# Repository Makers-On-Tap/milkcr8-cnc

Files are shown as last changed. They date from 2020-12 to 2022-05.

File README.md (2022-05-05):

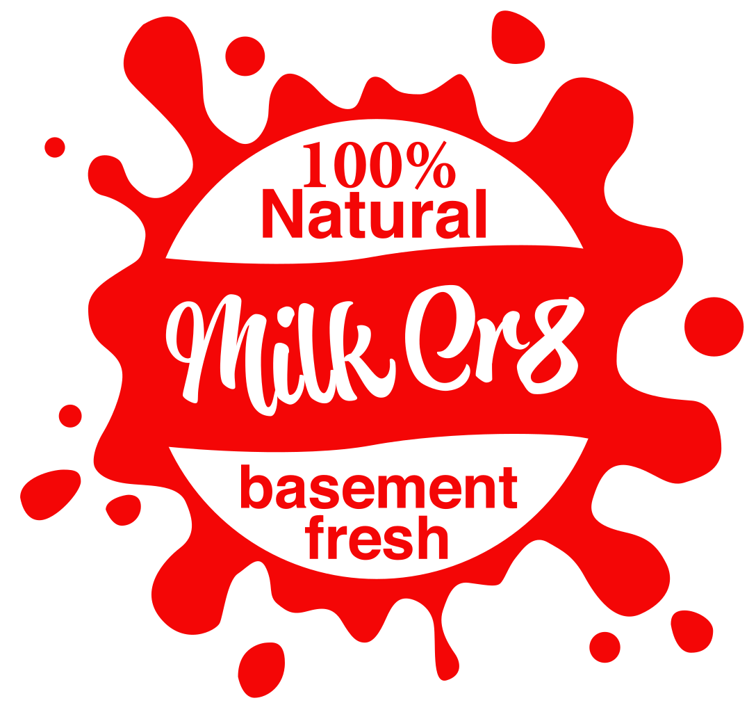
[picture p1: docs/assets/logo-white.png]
milkcr8_logo


# Welcome to the Milk Cr8 CNC Project
Home of the Milkcr8 Desktop CNC Machine!

Check out the [documentation site](https://www.milkcr8cnc.com)

This project uses mkdocs-material for the theme, the [reference guide for supported markdown features is available here](https://squidfunk.github.io/mkdocs-material/reference/#configuration)

Documentation files are located under the `docs` folder

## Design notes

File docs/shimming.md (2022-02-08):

# Shimming and Flattening the X Tube

The hot rolled mild steel tubing used for the X axis (and the Y axis) isn't always flat enough on the wide face for perfect mounting of the rails without some extra work. 

In one trial, there was variance of 0.01 inches across the wide face of the tube, with about 0.007" of variance over the width of the rail. 

First, we recommend checking each side to see if one is flatter than the other. Check it with a straight edge, and look for light coming through under the blade of the straight edge.

What looks like a small bump on the edges will still add up to too much difference in rail flatness to mount the Z axis without binding the rails.

## Ways to Mount the Rails Flat

Luckily, there are a few options if your X tube isn't flat.

1. Get someone to mill the face of your tube flat. 
2. Use epoxy to level the face of your tube.
3. Shimming the rails. (this is what we're talking about here)

## Shimming the Rails

Luckily, shimming the rails isn't hard, and can be done stably with commonly available materials.

Most grocery stores will sell [heavy duty aluminum foil](https://www.reynoldsbrands.com/products/aluminum-foil/heavy-duty-foil). 

This is inexpensive (though more expensive than regular aluminum foil) and is consistently 0.001" in thickness.

Aluminum soda cans have a thickness of 0.004". Soda can walls will be very sharp when cut, so proceed with caution.

The rails are 12mm wide, with a clearance of 3.5mm in the center for the M3 screws. So the width of the shim needn't be much wider than 4.25mm (12mm / 2 - 3.5mm / 2)

### Shimming With Foil

Fold a length of foil in half, and insert the folded seam under the low side of the rail. 

If you have a dial indicator, tighten a section of the rail and check the flatness over the short dimension of the top face. Loosen and add more shims as needed. Tightening screws before each measurement, and loosening to add more shim material.

### Shimming With Soda Cans

Cut the top and bottom off the can, and make one straight cut up the side so you can unroll the can flat. Use acetone to clean off the food-safe lining from the inside, and remove any ink that will come off the outside. 

Cut the can into 4-5mm wide strips, so the long edge is the circumference of the can. You should be easily be able to get eight strips from a standard can, which is enough for two strips under the entire length of each 300 mm rail. 

Insert one shim under the low side of the rail. Tighten, and measure. Add additional stock if needed, and repeat measurements until the rail is mostly flat along it's short dimension of the top face.

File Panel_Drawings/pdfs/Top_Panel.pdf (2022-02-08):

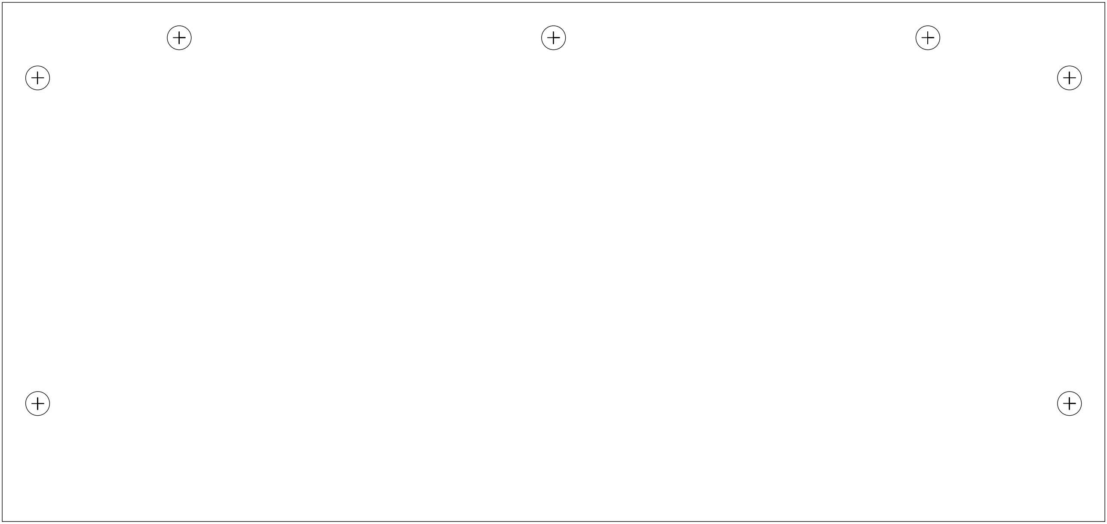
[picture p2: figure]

138mm

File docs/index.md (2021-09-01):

# Welcome to the MilkCrate CNC Project!

This site contains all the info and instructions you'll need to build your own desktop CNC mill!

If you're new to the project, check out the [About](about.md) page to learn the backstory of the MilkCrate CNC.

If you have some questions about it, check out our [FAQ](faq.md) page! Your question is most likely answered there.

Development and discussion of the project is done in the MilkCr8 CNC Discord server. https://discord.gg/qguQRYZAea

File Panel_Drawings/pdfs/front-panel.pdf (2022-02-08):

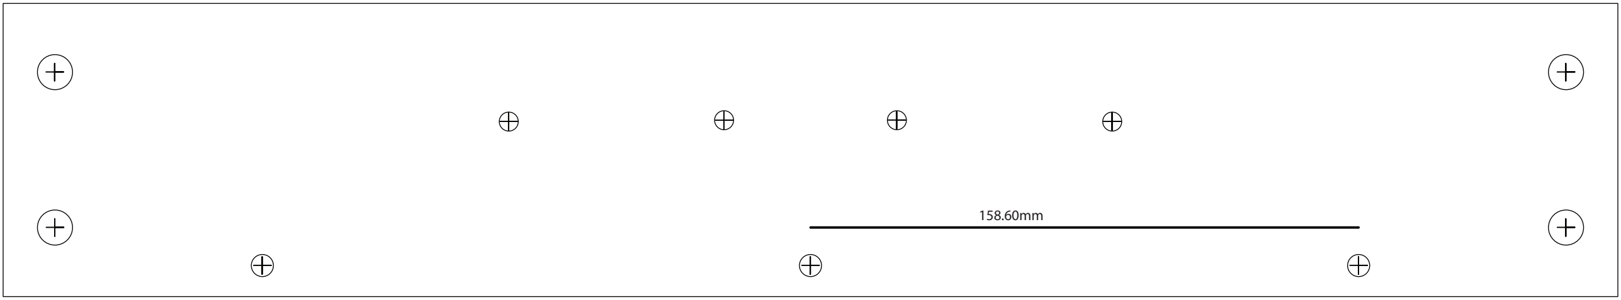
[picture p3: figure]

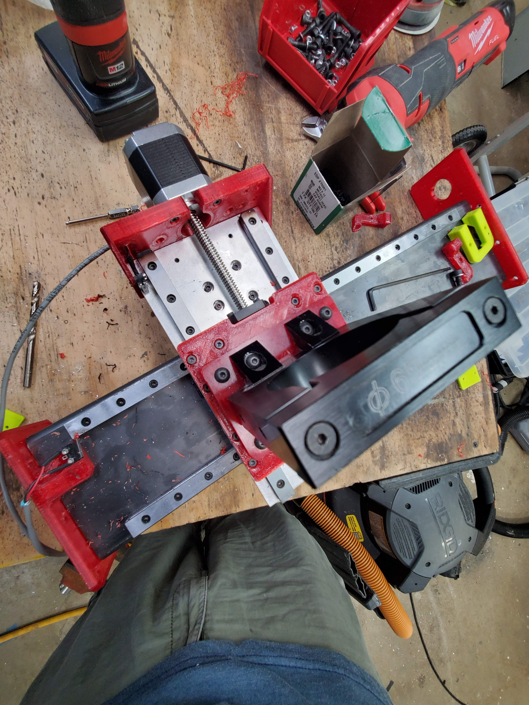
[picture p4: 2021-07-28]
docs/assets/images/img/xz_sub6.jpg

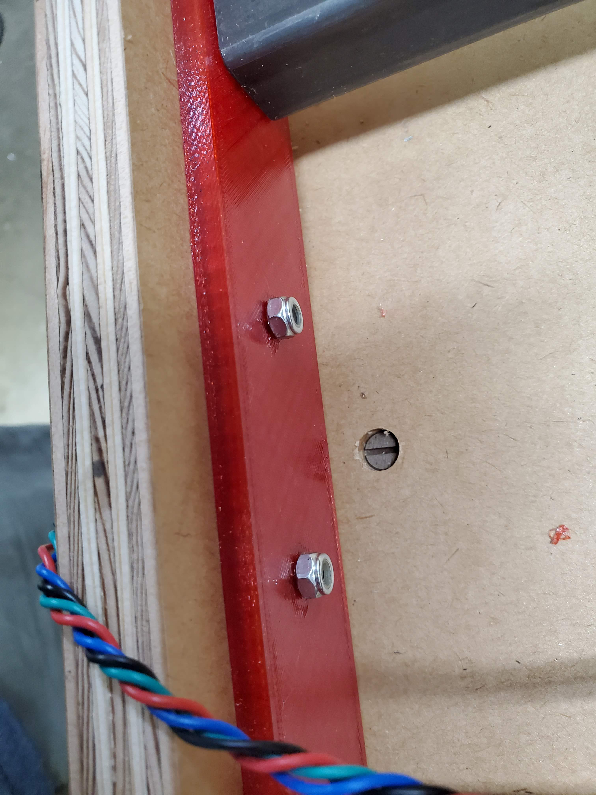
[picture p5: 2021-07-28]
docs/assets/images/img/y_box2.jpg

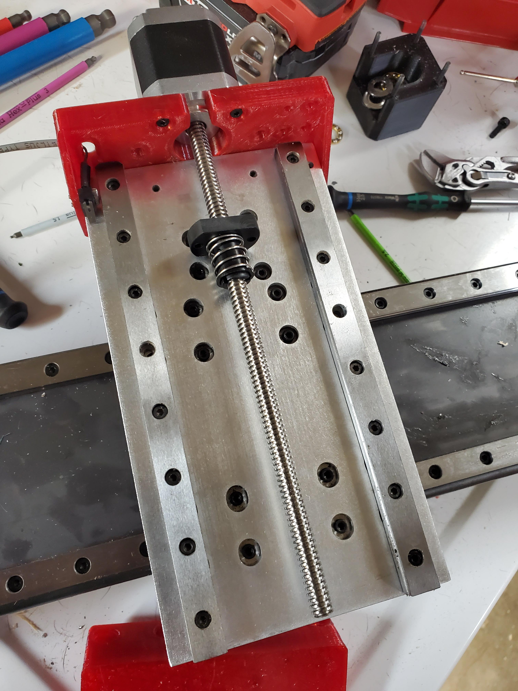
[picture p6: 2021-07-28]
docs/assets/images/img/xz_sub1.jpg

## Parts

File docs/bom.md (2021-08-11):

# Bill of Materials
Current BOM can be found in this [read only Google Sheet](https://docs.google.com/spreadsheets/d/1ViruGe-mIjATBrFZ_2N3Xh3YK8Kv0xZOzpvj6fFhka0/edit?usp=sharing). The BOM is considered semi-stable and but safe to order from.

# Source files and STL's
All parts to be made can be found here https://github.com/Makers-On-Tap/milkcr8-cnc

# Printed Parts List
All the non-jig [printed parts](https://github.com/Makers-On-Tap/milkcr8-cnc/tree/main/printed%20parts) are print 1 of each, unless otherwise noted in the filename (i.e. Hinge_6x.stl is 6 units)

You'll need two of each [jig](https://github.com/Makers-On-Tap/milkcr8-cnc/tree/main/printed%20parts/JIGS)

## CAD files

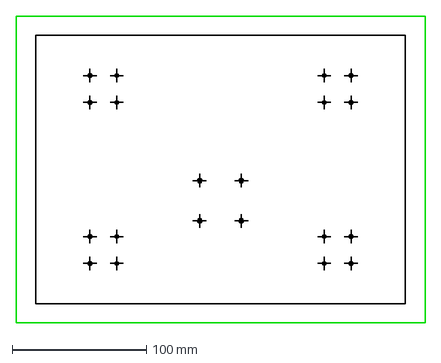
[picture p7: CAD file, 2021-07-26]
Panel_Drawings/dxf/bed_punch_template.dxf
304.8 x 228.6 mm

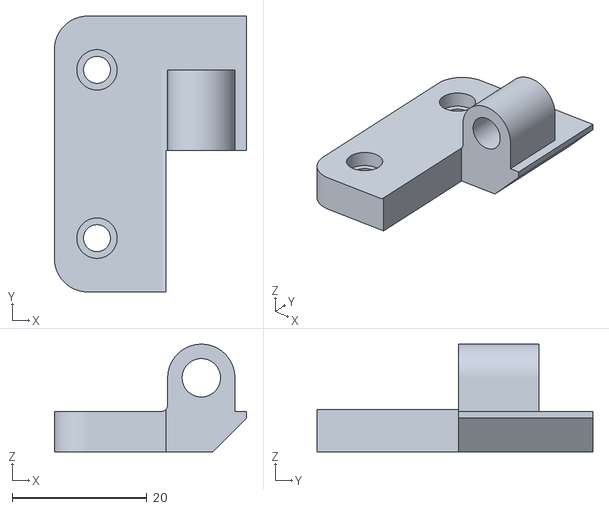
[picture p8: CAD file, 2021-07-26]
printed parts/Hinge_6x.stl
28.6 x 41.0 x 16.0

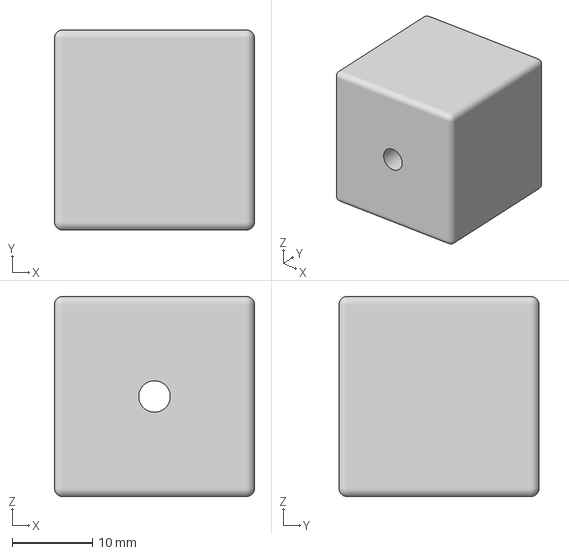
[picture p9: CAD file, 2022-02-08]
printed parts/JIGS/M3TapGuide0.4mm.3mf
25.0 x 25.0 x 25.0 mm

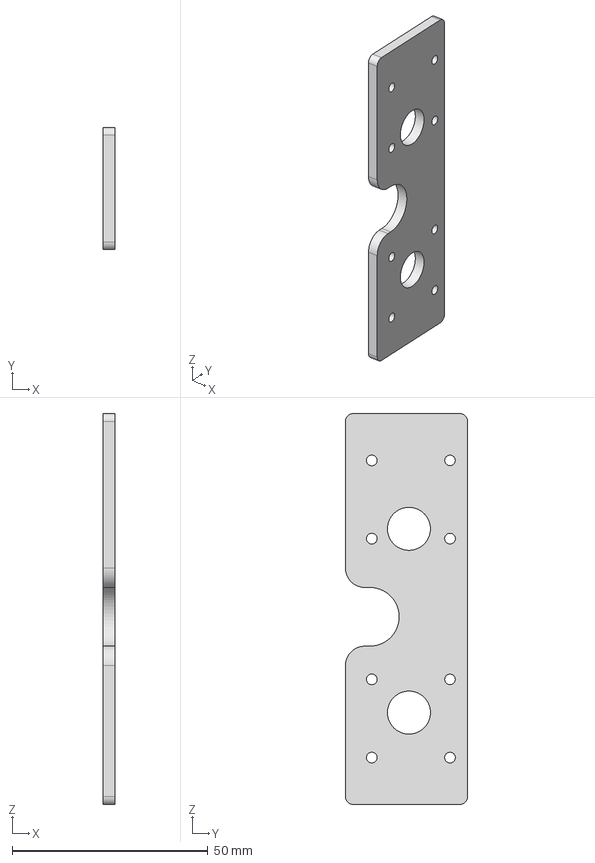
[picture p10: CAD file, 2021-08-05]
printed parts/STEP/Z_Spacers_x2.step
3.18 x 31.3 x 100.0 mm

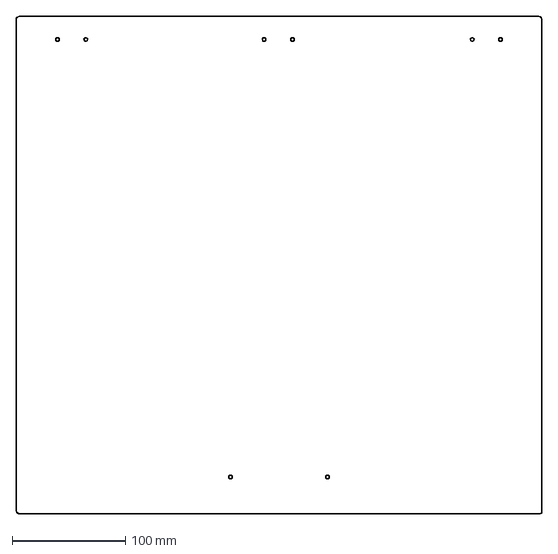
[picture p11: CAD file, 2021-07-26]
Panel_Drawings/dxf/Window_qtr_in_acrylic.dxf
464.0 x 439.0 mm

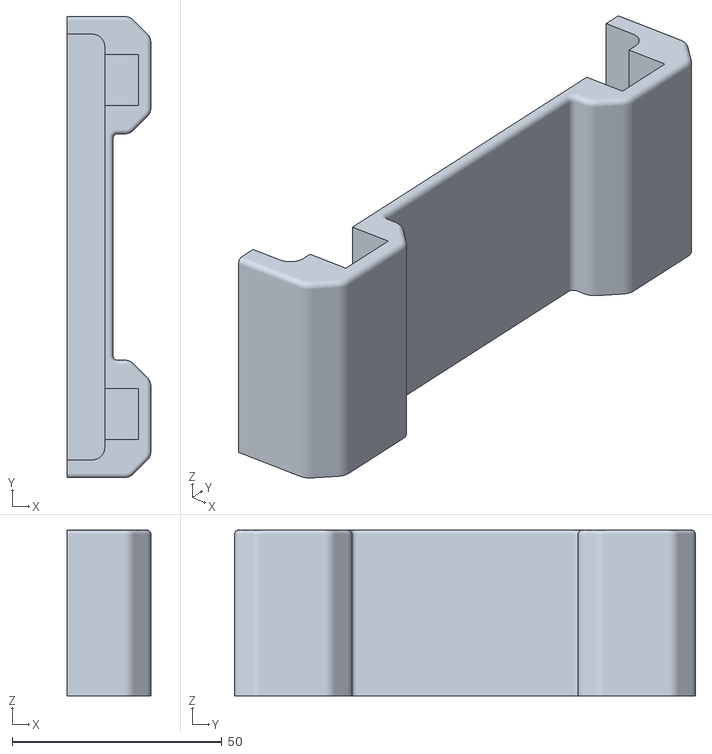
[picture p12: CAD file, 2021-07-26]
printed parts/JIGS/Jig_X_Rail_x2.stl
20.0 x 110.0 x 39.6

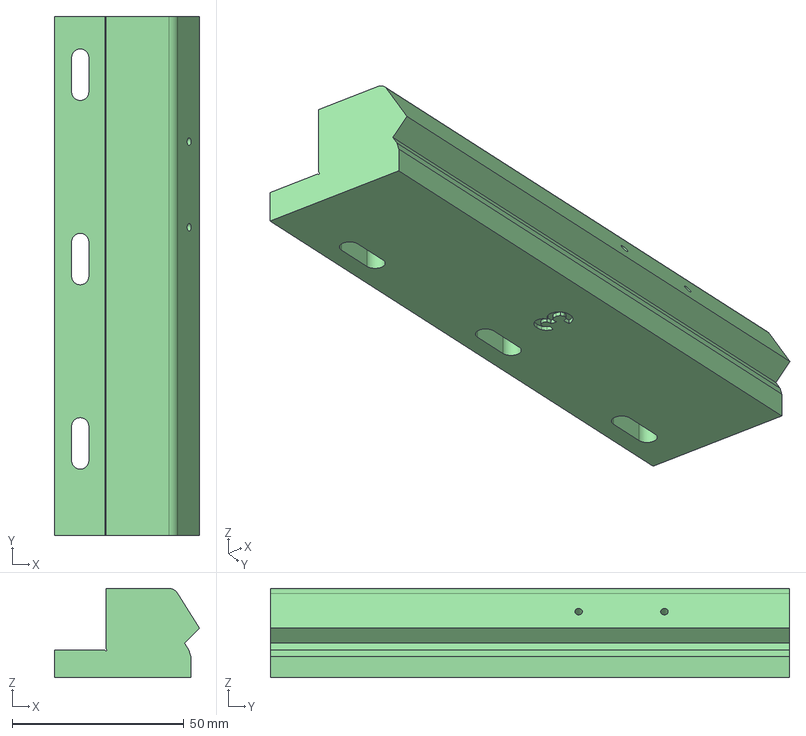
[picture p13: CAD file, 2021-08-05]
printed parts/STEP/WinMountTop_Right3.step
42.3 x 151.4 x 26.0 mm

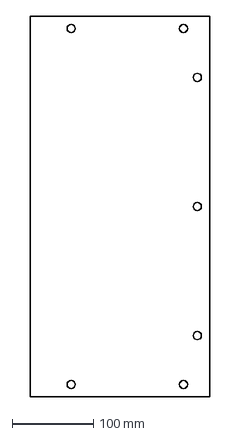
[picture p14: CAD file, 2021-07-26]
Panel_Drawings/dxf/Top_Panel.dxf
220.0 x 467.2 mm

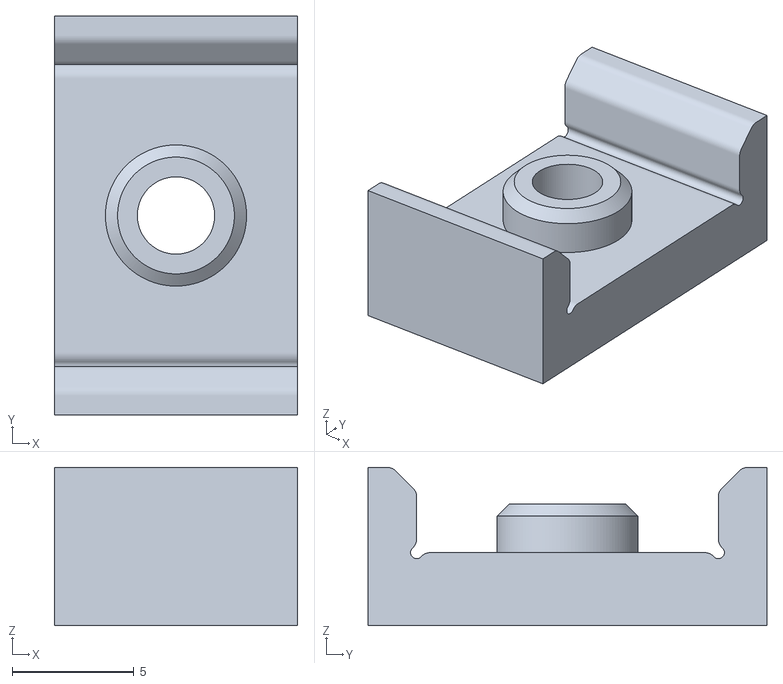
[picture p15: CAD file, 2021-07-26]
printed parts/JIGS/Jig_RailPunch.stl
10.0 x 16.4 x 6.50

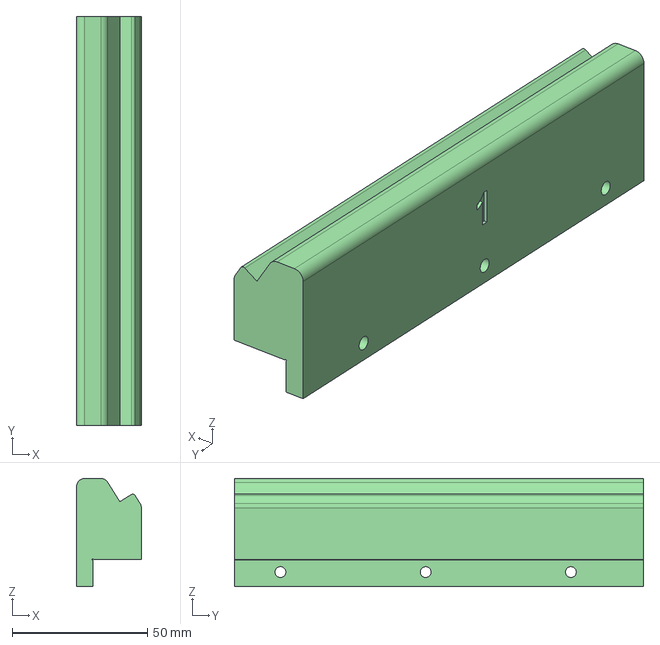
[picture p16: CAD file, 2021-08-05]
printed parts/STEP/WinMountBot_Left1.step
24.0 x 151.4 x 40.0 mm

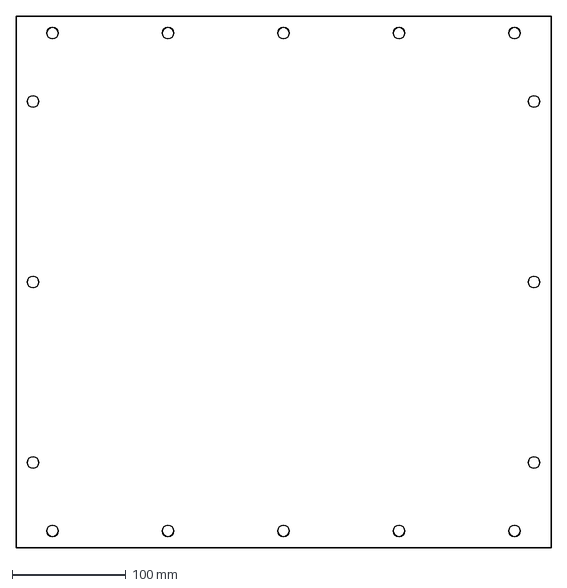
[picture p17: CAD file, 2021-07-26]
Panel_Drawings/dxf/Bottom_panel.dxf
469.9 x 467.2 mm

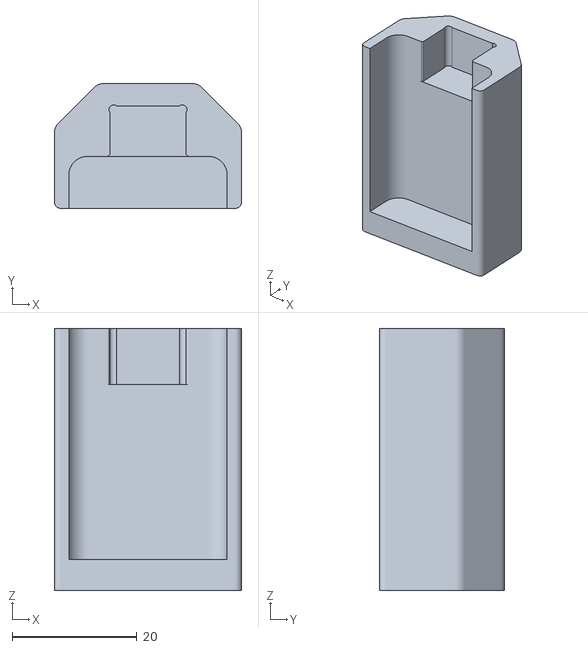
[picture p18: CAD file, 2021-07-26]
printed parts/JIGS/Jig_Y_Rail_x2.stl
30.0 x 20.0 x 42.0

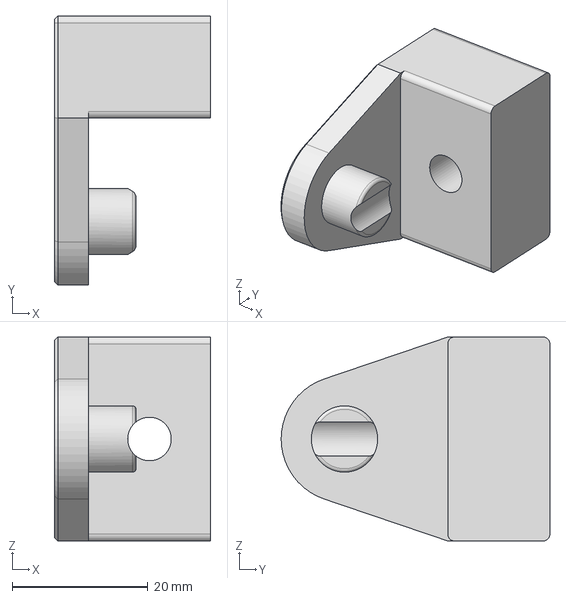
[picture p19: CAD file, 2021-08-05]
printed parts/STEP/Jig_Dowel_Pins.step
23.0 x 39.5 x 30.0 mm

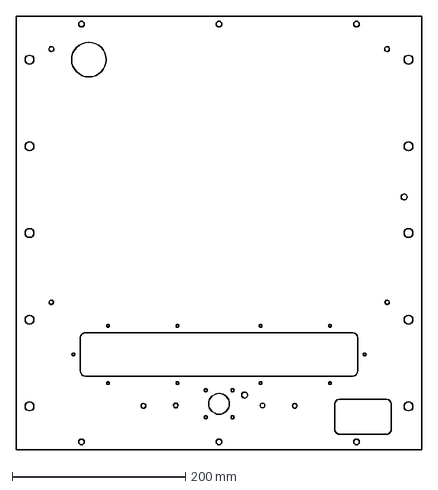
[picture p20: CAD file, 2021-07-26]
Panel_Drawings/dxf/Back_panel.dxf
467.2 x 500.0 mm

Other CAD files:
printed parts/JIGS/Jig_Dowel_Pins_18MM_ply.stl
Panel_Drawings/dxf/Front_panel.dxf
printed parts/STEP/Jig_RailPunch.step
Panel_Drawings/dxf/side_panel.dxf
Panel_Drawings/dxf/Motor_side_panel.dxf
printed parts/DustCover_Left.stl
printed parts/DustCover_Right.stl
printed parts/STEP/DustCover_Left.step
printed parts/STEP/DustCover_Right.step
printed parts/STEP/Hinge_x3.step
printed parts/STEP/Jig_X_Rail_x2.step
printed parts/STEP/Jig_Y_Rail_x2.step
printed parts/STEP/Vac_Port.step
printed parts/STEP/WinMountBot_Mid2.step
printed parts/STEP/WinMountBot_Right3.step
printed parts/STEP/WinMountTop_Left1.step
printed parts/STEP/WinMountTop_Mid2.step
printed parts/STEP/Window_Handle.step
printed parts/STEP/X_Lead_Nut_Mount.step
printed parts/STEP/X_Thrust_Block.step
printed parts/STEP/X_Tubes_LeftIdler.step
printed parts/STEP/X_Tubes_RightMotor.step
printed parts/STEP/Y_Lead_Nut_Mount.step
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

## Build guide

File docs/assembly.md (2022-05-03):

# Assembly

## Table of Contents

* [Prep Work](#Prep-Work)
	* [Tapping and Assembling the X and Z Axis Assembly](#x-and-z-axis-sub)
	* [Assembling the X and Z Axes](#assembling-the-z-and-z-Axes)
* [Making the Cr8](#cr8-atart)
	* [Cr8 Assembly](#cr8-assembly)
* [Y Axis Start](#y-axis-Start)
* [Window](#window)
* [Spindle Mount](#spindle-mount)

## Prep Work

Read through all the directions before you start. You can batch out a few things, like drilling and tapping before you do assembly. Other items are more sensitive to order. We've tried to point that out when it may not be obvious. 

3d-print all your 3D printed parts per the [instructions](printing.md).

Make sure you have two of all the jigs marked 2x in the Fusion360 Project. Pre-drill all the holes. Most can be predrilled with a 1/4" bit. Use an 1/8" bit for smaller holes. The only holes that should be pre-drilled smaller than 1/8" are for the M2 screws that hold in the limit switches.

## X and Z axis Sub

### Punch, Drill and Tap the X-Axis 

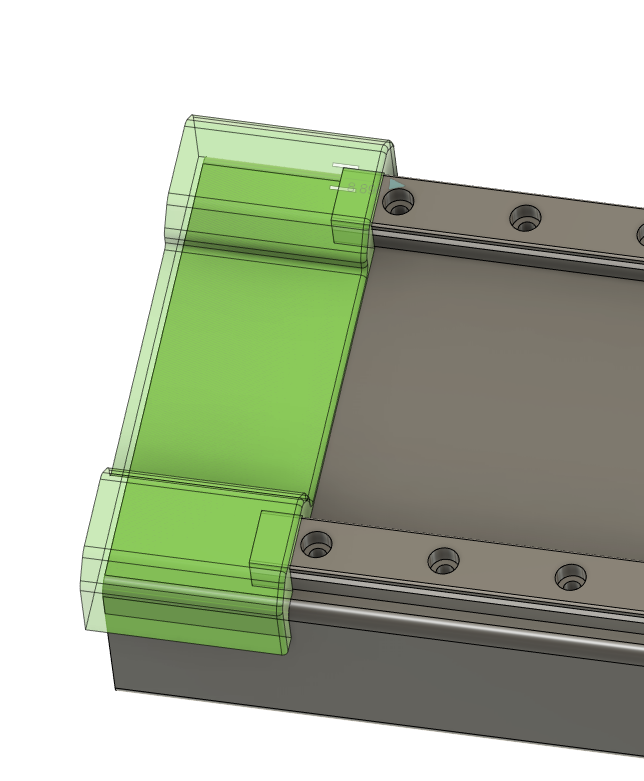
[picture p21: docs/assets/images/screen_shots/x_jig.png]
x_jig


Take a look at your 4x1.5x18" steel tube and see if one side is flatter along the 4" length than the other.

If one side is noticeably flatter, set up your printed X-Axis jigs and linear rails on that side. 

We recommend using a 3.5 mm transfer punch to make a light mark for each of the holes, and then enlarging those holes slightly with a center punch. 

Drill all 16 holes for each rail, and tap with an M3 0.5 tap and plenty of tapping fluid. There is an M3 tap guide in the jigs folder on the github to help keep the tap straight. You may have to adjust the scale slightly depending on the settings and nozzle size on your 3D printer.

At this point, you can start screwing down your rails to the tube with M3x10 SHCS and check if the rails are flat. It's not uncommon for the rails to both be tilted in toward the center of the axis. If this is the case (or if they are otherwise out of parallel with each other) check out the [shimming](shimming.md) guide.

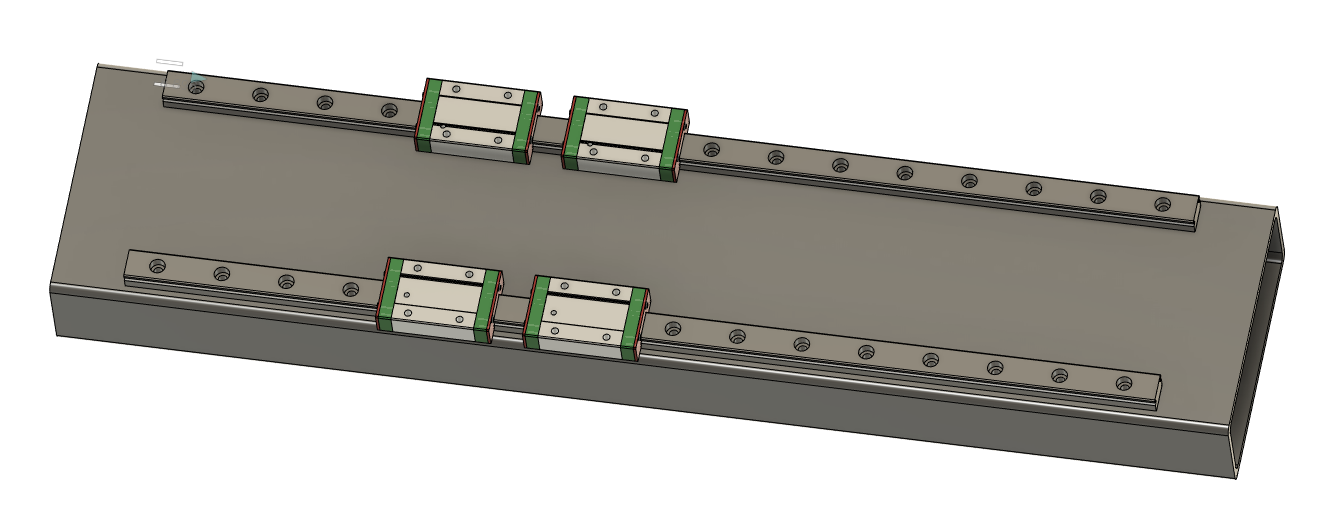
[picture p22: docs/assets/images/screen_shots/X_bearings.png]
x_bearings


### Assembling the X and Z Axes

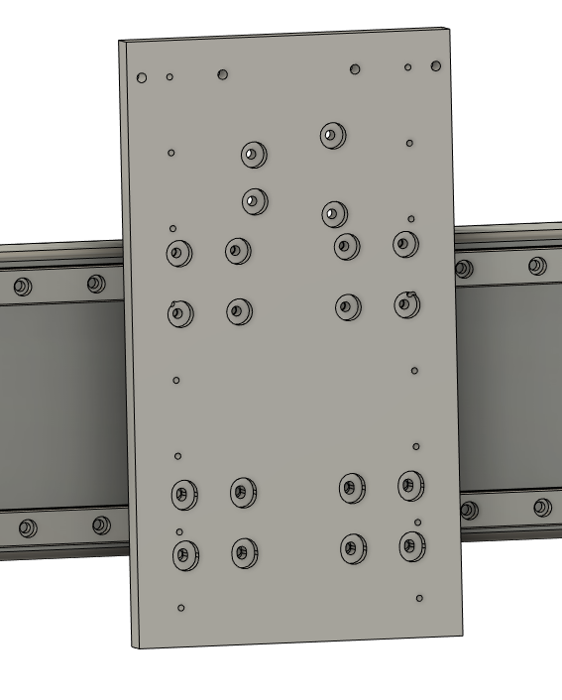
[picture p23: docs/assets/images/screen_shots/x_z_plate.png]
x_z_plate


Use 16 M3x10 SHCS to bolt the Z to X Plate to the carriages.  

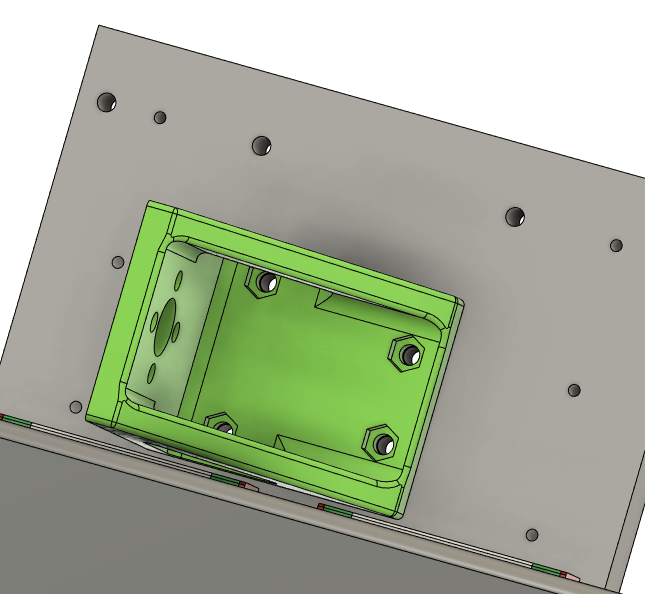
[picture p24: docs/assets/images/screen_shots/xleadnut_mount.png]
x_leadnut


M3 nuts pressed into X Lead Nut Mount.
M3x12 SHCS to bolt the X Lead Nut Mount to Z to X plate.

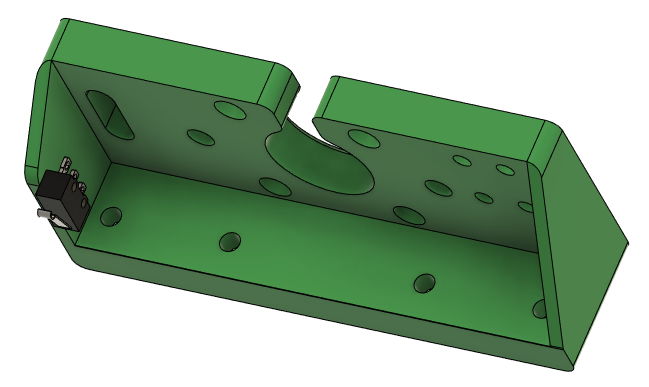
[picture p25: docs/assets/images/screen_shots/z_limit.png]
Z_limit


M2x12mm bolts to attach the limit switch to the Z Linear Motor Mount. You cannot attach the limit switch once the Z Motor Mount is attached to the Z to X Plate.
Solder wires before bolting. The "Normally Closed" (NC) configuration is recommended for best safety practices.
Run wire for the Z limit switch through slot in the Z Linear Motor Mount. 

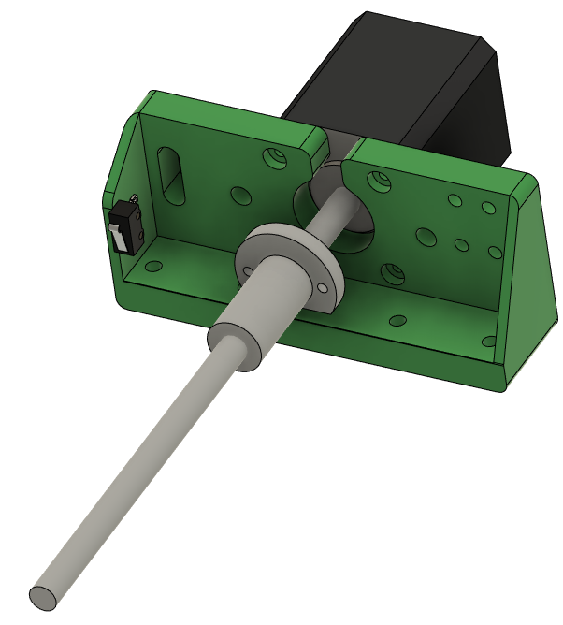
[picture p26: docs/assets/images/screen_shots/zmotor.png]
Z_motor


M3x10 screws into motor, through the Z Linear Motor Mount. You cannot attach the Z Motor after the Linear Motor Mount is attached to the Z to X Plate.  
Make sure lead nut is mounted now, it's a real pain to mount it later. 

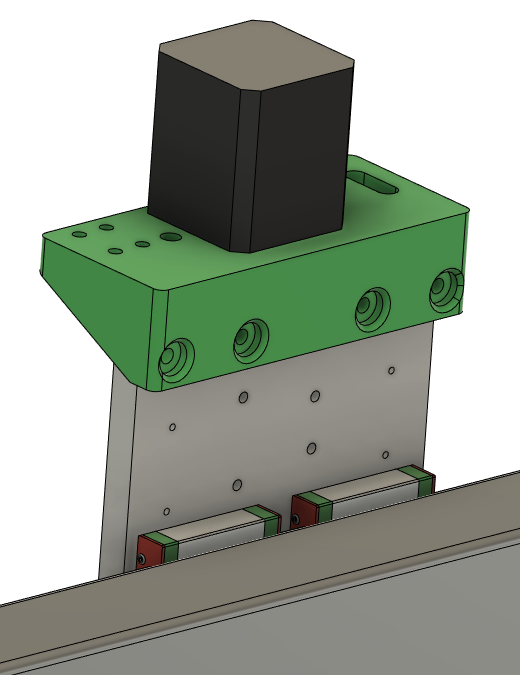
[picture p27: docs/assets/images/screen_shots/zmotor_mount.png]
Z_motor_mount


M4x12 SHCS to through the Z Linear Motor Mount to the Z to X Plate  
Use M4 self tapping screws if using plastic plates

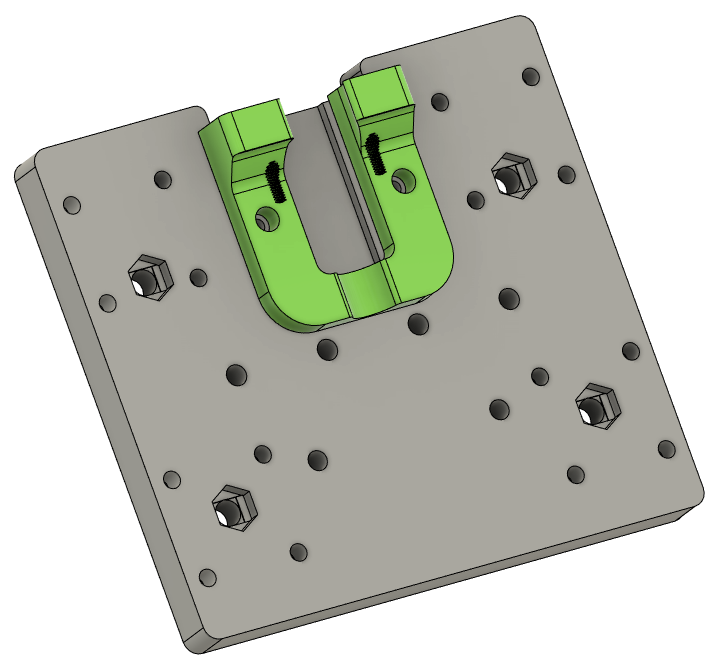
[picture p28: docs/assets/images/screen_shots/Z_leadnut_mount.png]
Z_leadnut


Use M4x12 SHCS to attach the Z Lead Nut Mount to the Z Plate.
Insert M5 nylock nuts into the Z Plate now. It is impossible to insert these once the Z Plate is mounted on the carriage. If they are loose, you can hold them in place with M5 screws until you attach the tram plate and router mount.

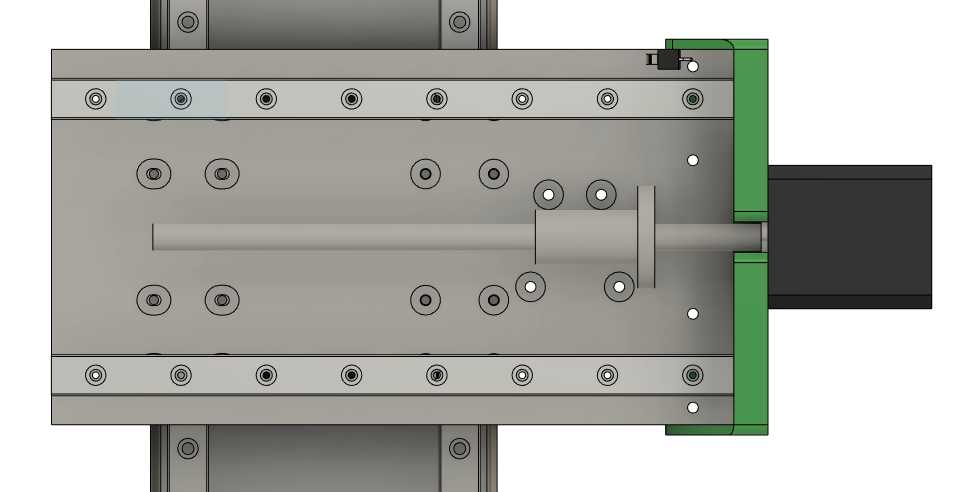
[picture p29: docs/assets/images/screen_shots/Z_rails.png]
Z_rails


Use M3x10 SHCS, or M3 self-tapping screws to attach the Z Linear Rails to the Z Plate.

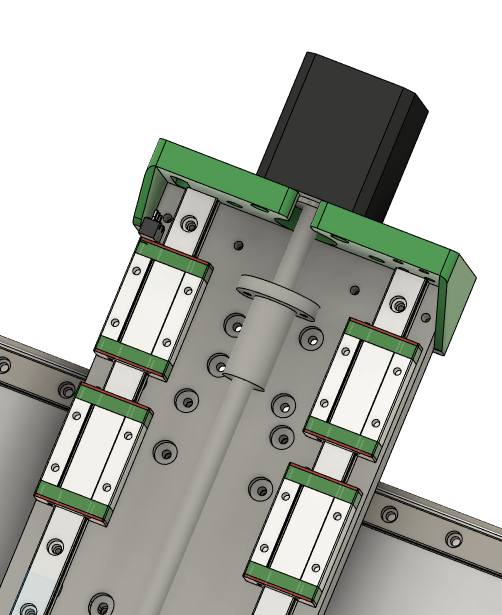
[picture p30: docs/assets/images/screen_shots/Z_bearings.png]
Z_bearings


Put two Z bearings on each Z rail.

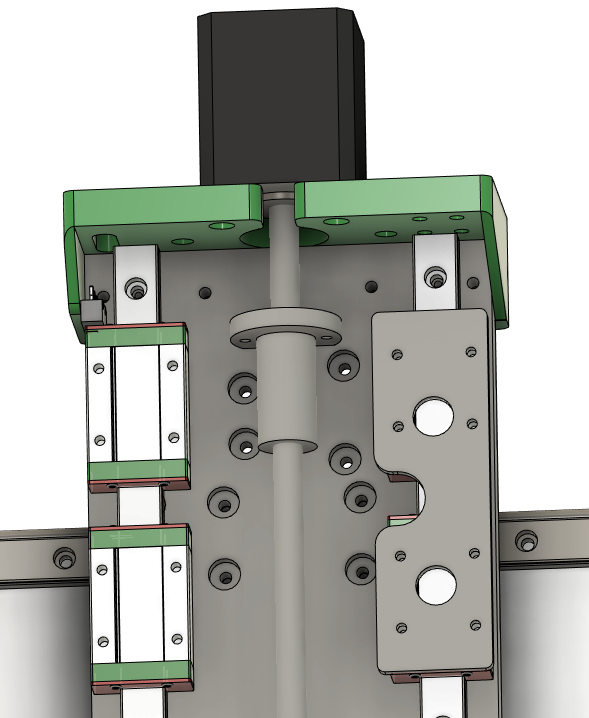
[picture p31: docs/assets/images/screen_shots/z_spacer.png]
Z_spacer


Put 1 Z Spacer over each set of bearings.
Drill out the bolt holes if needed to make sure the M3 bolts slip through cleanly  

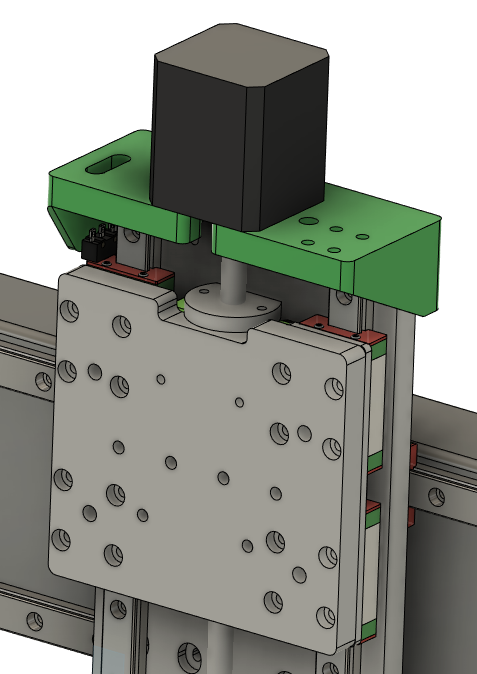
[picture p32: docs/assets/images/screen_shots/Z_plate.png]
Z_plate


Use M3x10 SHCS attach the Z Plate to the bearing blocks through the spacers.

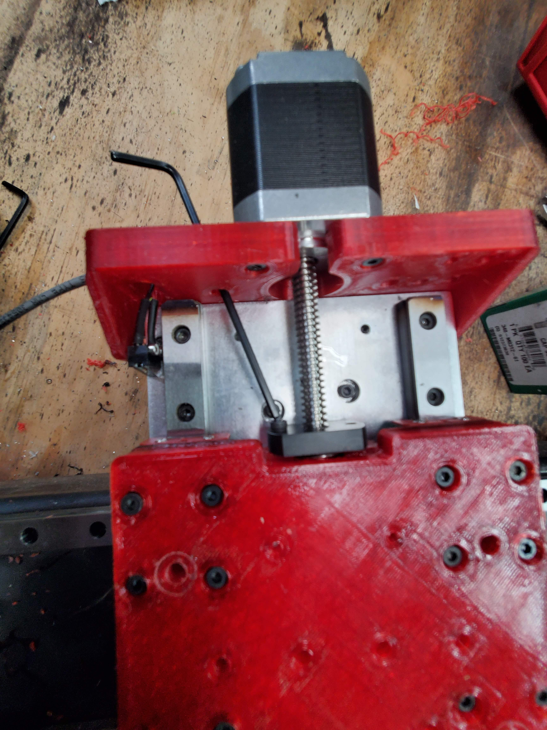
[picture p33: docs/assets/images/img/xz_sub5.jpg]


Use M3x10 SHCS tp attach the Z Lead Nut Mount to the Z Plate. Use the holes in Z Linear Motor Mount to slip allen key through and access bolts. You may have to rotate the lead screw to properly align the Z Lead Nut Mount in order to screw in the bolts.

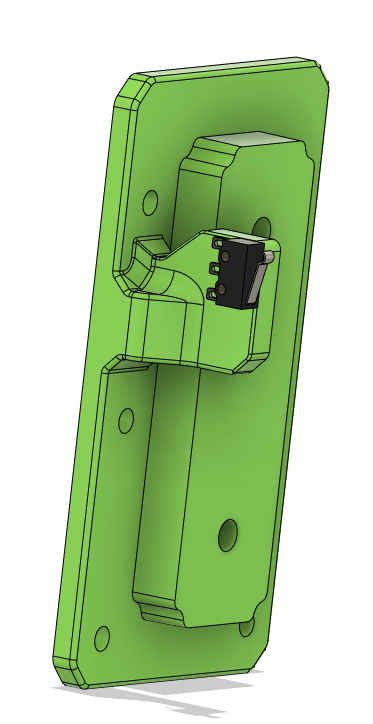
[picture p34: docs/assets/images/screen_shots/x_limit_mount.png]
X_limit


Solder the wires to the X limit switch and attach the X limit switch to the X Tube Left Idler with M2 screws. Do not attach the left X Tube Left Idlder to the X Tube at this time.

## Cr8 Start

Check the length of your X-tube. Midwest Steel has a tendency to cut the tubes 1/8" long. So you'll either need to file that down, or increase the width of the front, back, top, and bottom by 1/8" to compensate. 

A soft recommendation is to get the crate parts cut on a CNC. There are a lot of holes to drill and it's easier to get them all aligned if it's done by a computer. That said, there are also large format [PDFs](../Panel_Drawings/pdfs) to print and attach to the panels with spray adhesive that work as good guides. It's very possible to make it with hand-drilled holes in the crate, it's just harder.  

### Cr8 Assembly

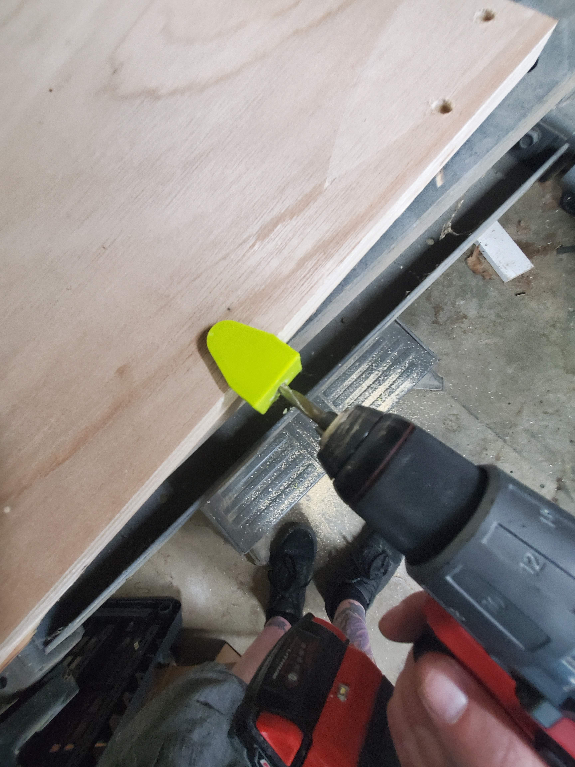
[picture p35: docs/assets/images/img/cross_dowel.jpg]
Cross Dowel


Use the dowel jig in the large holes on the frame drill the holes on the edge that the 1/4" bolts will go through and thread into the dowel nuts.

Drill the holes about 10mm past the dowel nut hole to allow for bolt clearance

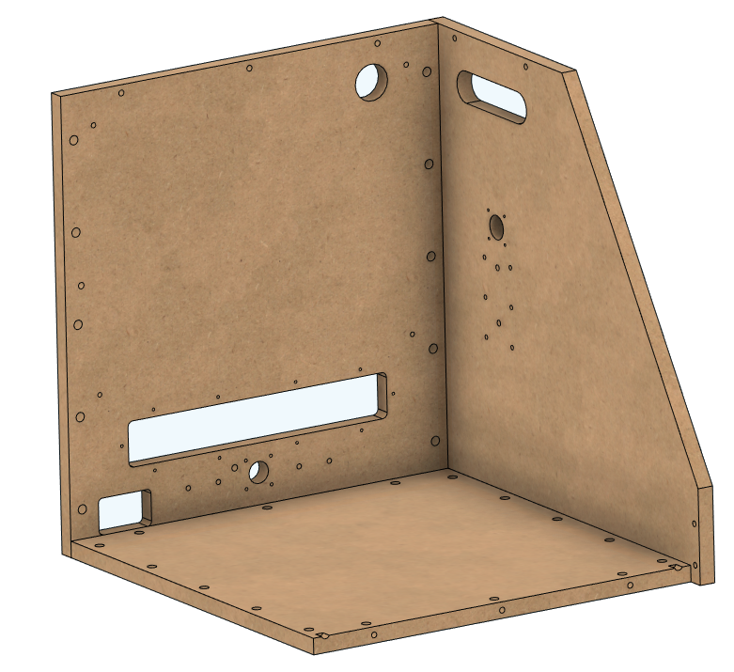
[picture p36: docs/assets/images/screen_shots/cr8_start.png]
Cr8


Build up Cr8 with 3 sides like this, the right side (from the front), the bottom, and back.

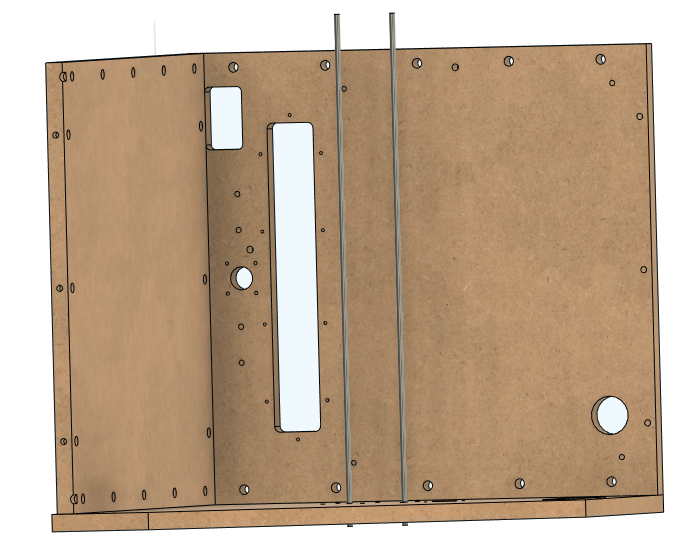
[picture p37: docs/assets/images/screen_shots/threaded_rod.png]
X-tension


Put lock washer, and nuts on one end of each of 2 threaded rods  

Put the two threaded rods through the X holes on the right side of the crate.

Lie the crate on the right side, with the threaded rod, washer, and nuts off the table, so it lies flat.

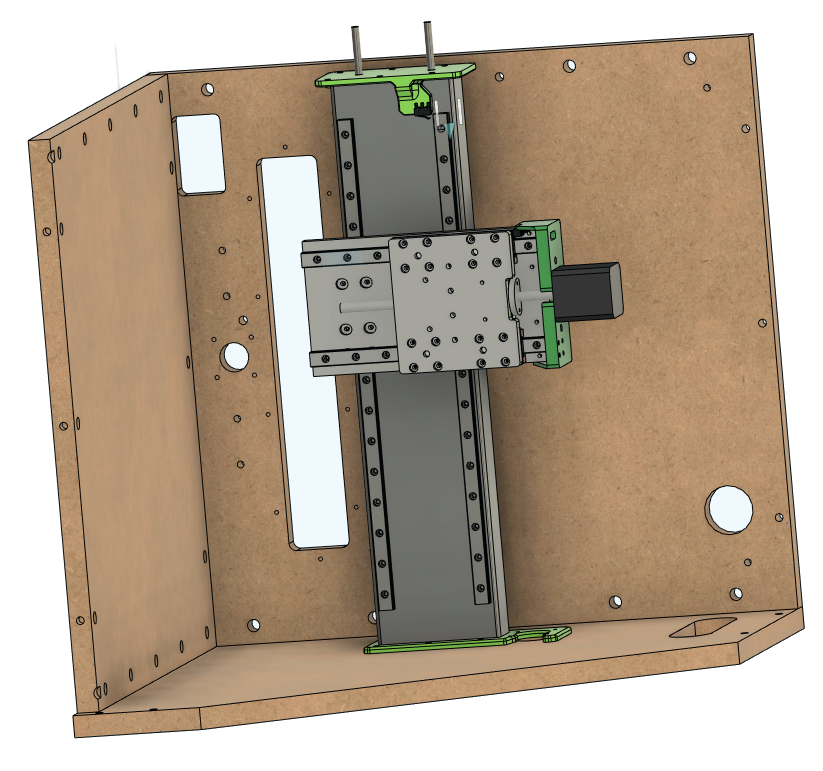
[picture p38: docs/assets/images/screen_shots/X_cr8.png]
X Cr8


Attach the X Tube Right Motor Cap to the right side of the X Tube. Sometimes the cap will need to be pounded in with a mallet, if it's tight, use a 2x4 over the plastic to avoid damaging it.

Slide the X-Z Sub-Assembly over the threaded rods all the way down. This can be a little fiddly but this is the easiest way. Thread the threaded rod through the X Tube Left Idler cap, and then place the X Tube Left Idler cap over the open left end of the X Tube, use the 2x4 and mallet method to secure it.

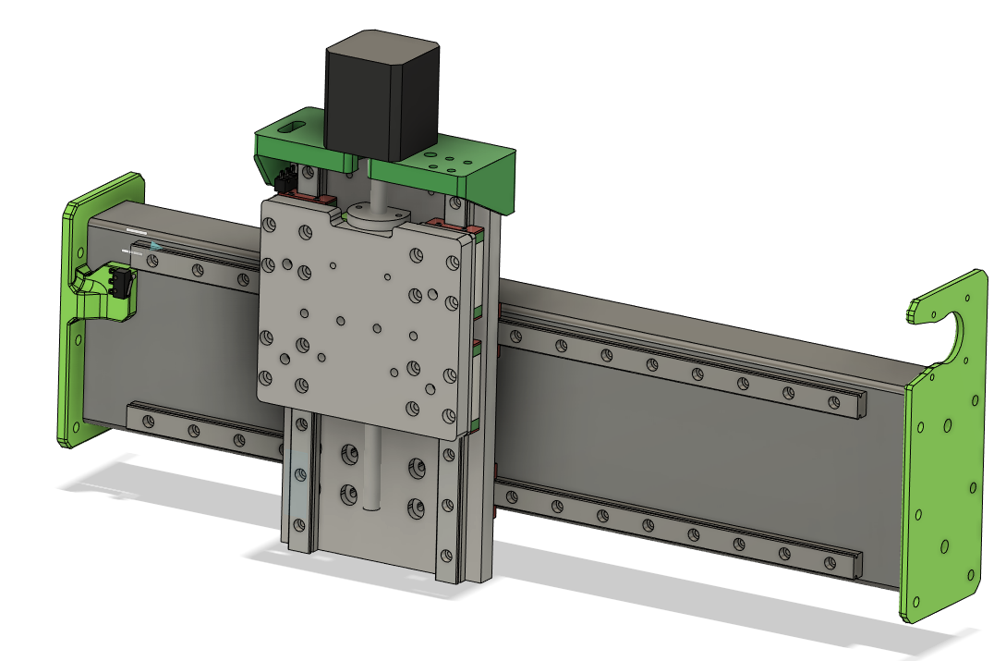
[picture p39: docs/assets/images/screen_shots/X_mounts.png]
X Mounts


Attach the left side of the crate. Add a lock washer and nut to each threaded rod on the left side. 

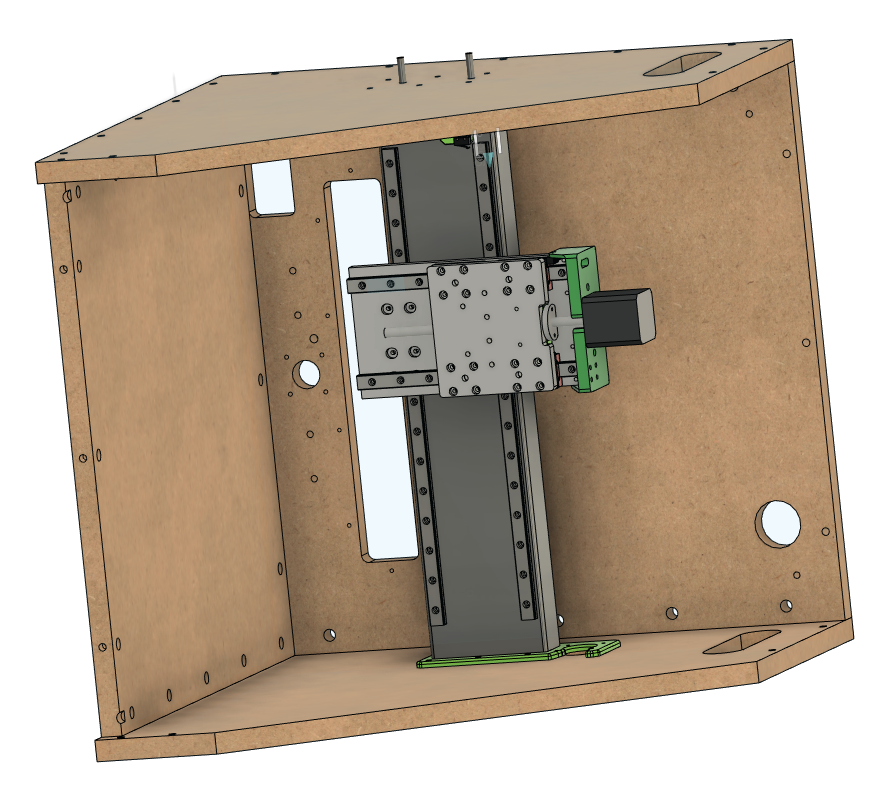
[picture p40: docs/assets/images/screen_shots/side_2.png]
Cr8 Side 2
 

## Y Axis Start

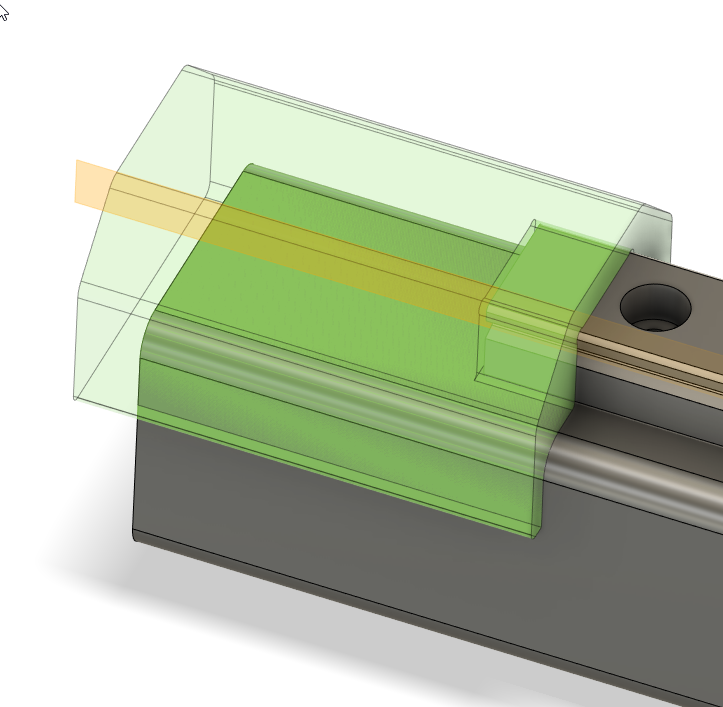
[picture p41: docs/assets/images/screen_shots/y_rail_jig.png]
Y Rail Punch


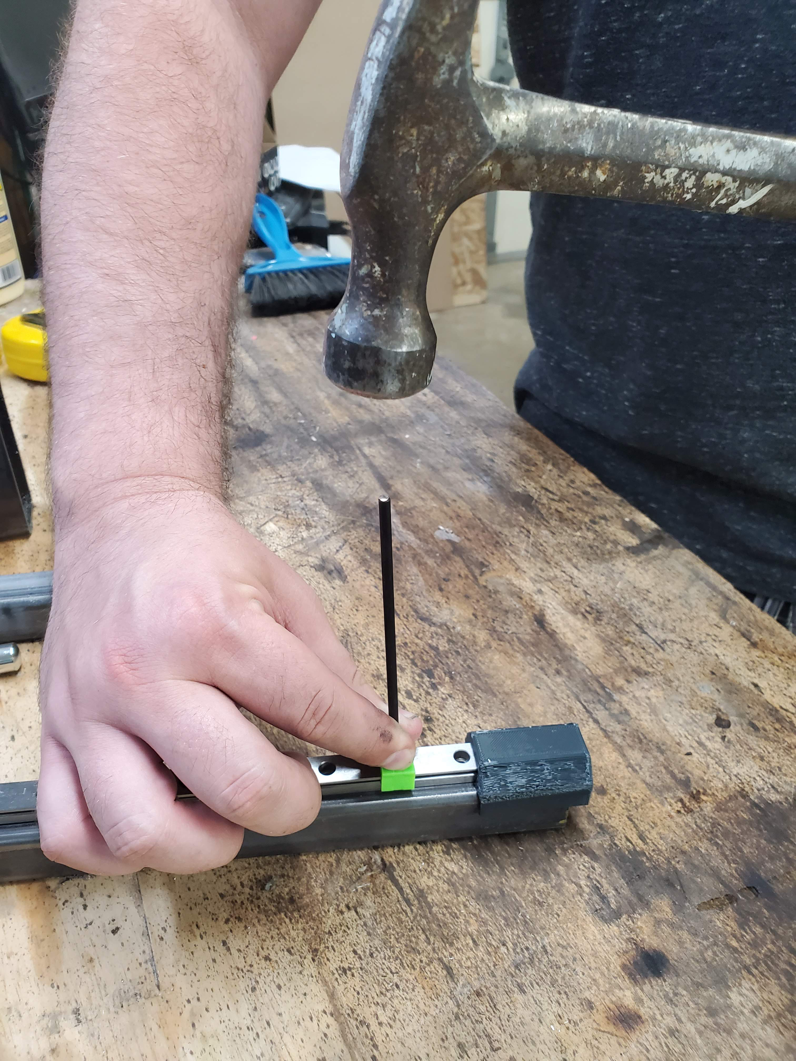
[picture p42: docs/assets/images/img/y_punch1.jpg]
y punch


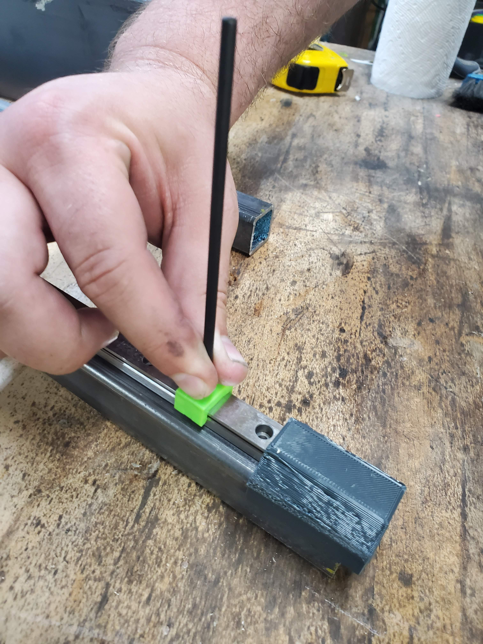
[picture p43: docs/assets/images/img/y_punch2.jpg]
y punch


We recommend using a 3.5 mm transfer punch to make a light mark for each of the holes, and then enlarging those holes slightly with a center punch. You can also use the rail punch jig to help align the holes.

Drill, and tap all holes. Use the tap jig as before, if you would like some help keeping the tap straight.

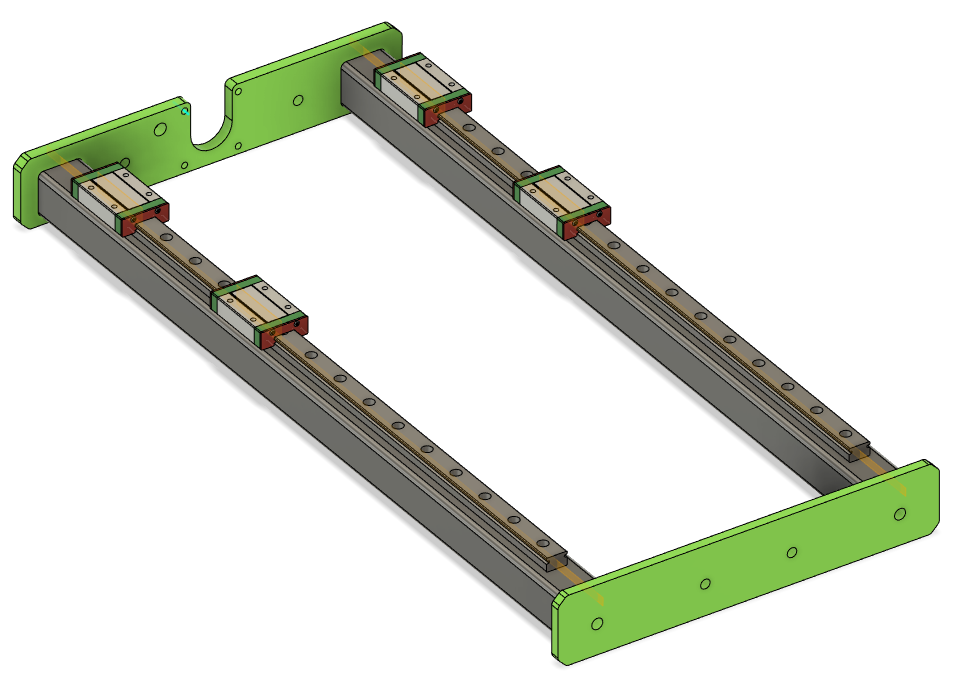
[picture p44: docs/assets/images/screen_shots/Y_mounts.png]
Y Axis Mounts


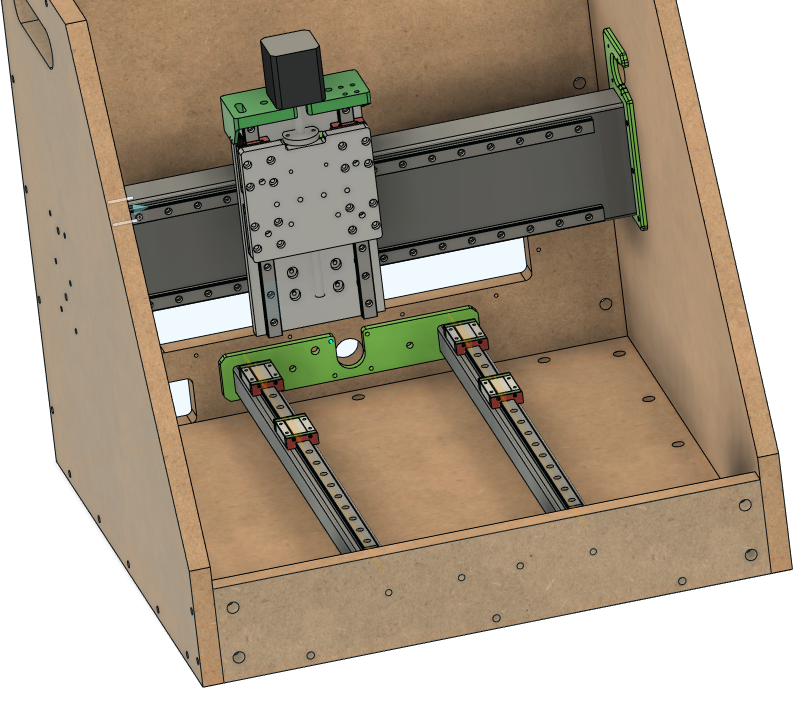
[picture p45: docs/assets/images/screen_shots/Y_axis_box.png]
Y Axis Box


Use M5x25 SHCS in the middle holes of the mounts, secure with a M5 lock nut on the opposite side.  

Slide the last two threaded rods in the outer holes through the tubes. Ive found it can be helpful to lay the frame on it's back so you are droppin the threaded rod through the holes.  

Like with the X tube, it's easiest to thread the threaded rod through only one plastic tube cap, and to leave the other side of the tube open. Once the threaded rod is through the tube cap, thread it through the other cap, and press that threaded tube cap on to the tubes. Attach the remaining cap and tubes to the crate. 

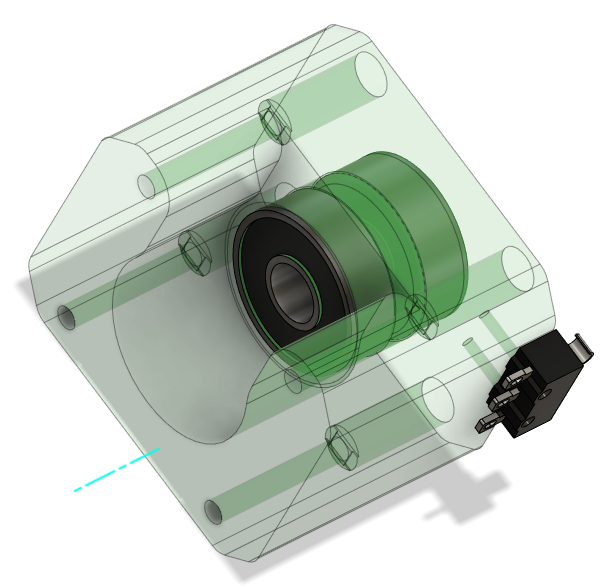
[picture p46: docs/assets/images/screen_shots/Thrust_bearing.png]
Thrust_bearing


Press 1 608 bearing into the front and back of each thrust block for the X and Y axes.  

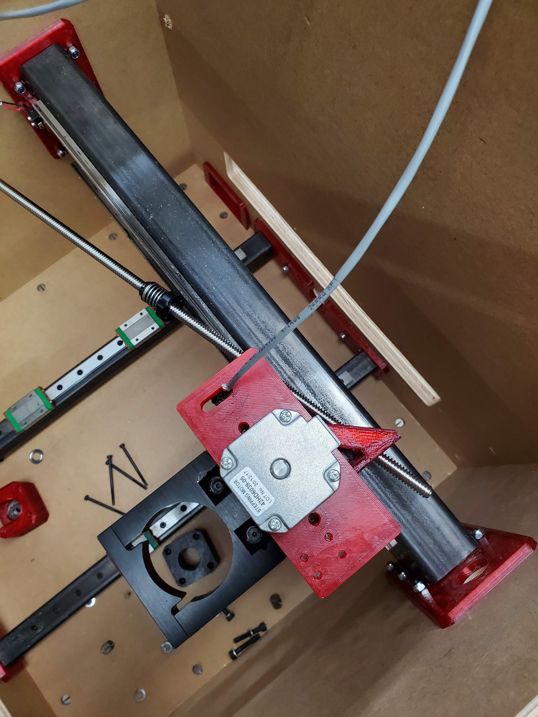
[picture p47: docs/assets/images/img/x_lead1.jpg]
x lead


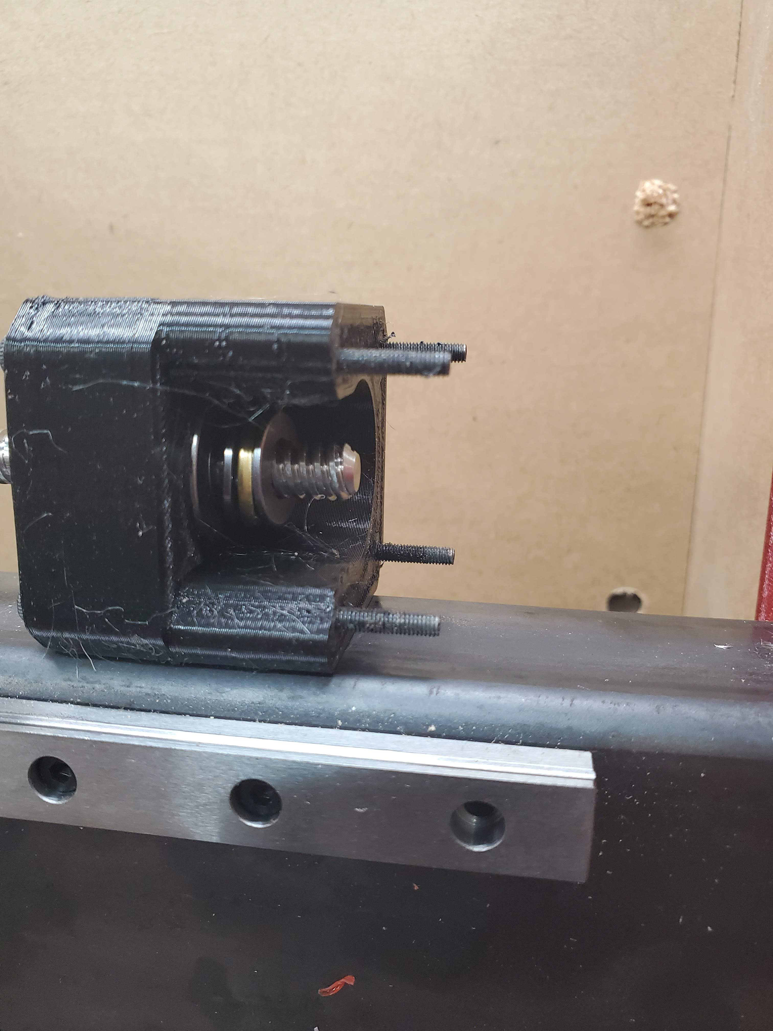
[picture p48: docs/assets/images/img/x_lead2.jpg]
x lead


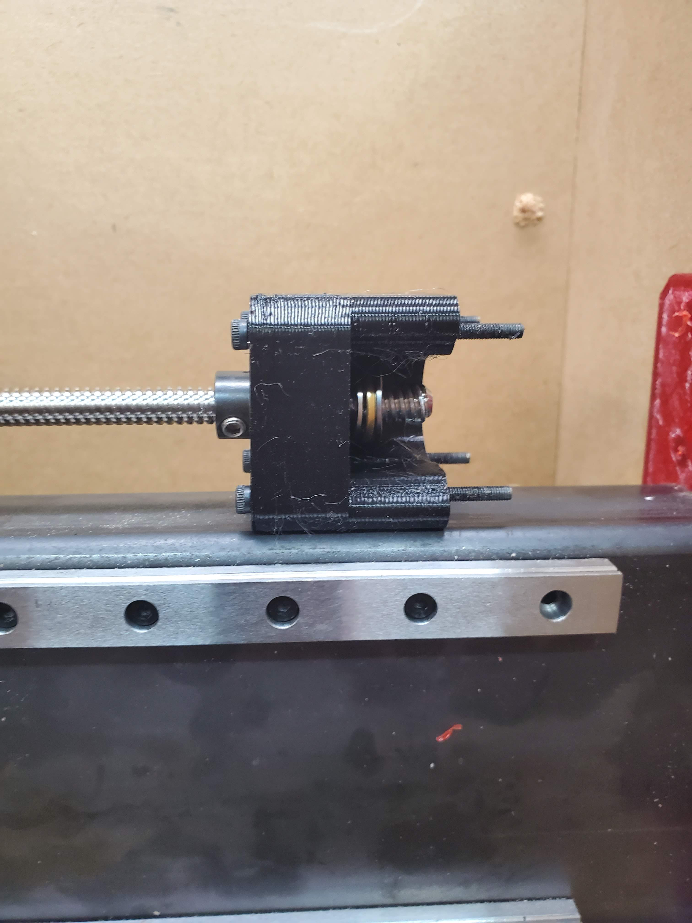
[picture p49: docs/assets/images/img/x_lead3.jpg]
x lead


Put the coupler on the motor shaft 10.5mm (ish) from the motor face

Slide the locking shaft collar and one M8 washer onto the leadscrew and then slide the leadscrew through the thrust block.

On the inside of the thrust block, slide the thrust bearing stack onto the lead screw and then tighten the coupler onto the lead screw.

Use 4 - M3x50 SHCS to bolt through the thrust block to the motor

Pull the lead screw away from the motor and press the shaft collar against the thrust block while tightening the set screw. - the goal is to remove the possibility for axial play. 

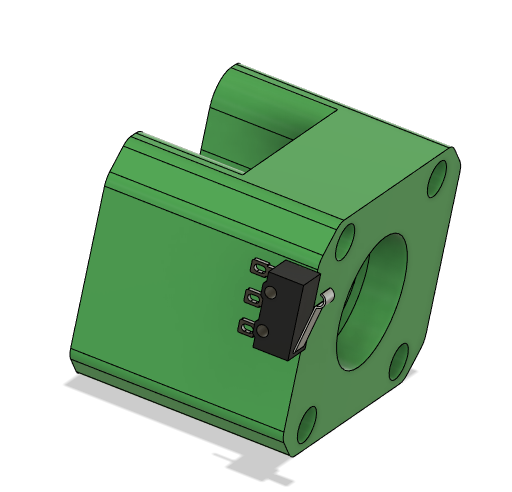
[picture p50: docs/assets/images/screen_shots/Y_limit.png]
Y Axis limit


Solder the wires for the limit switch and use an M2x12 SHCS to bolt it the thrust block with 2 small holes in the side.  

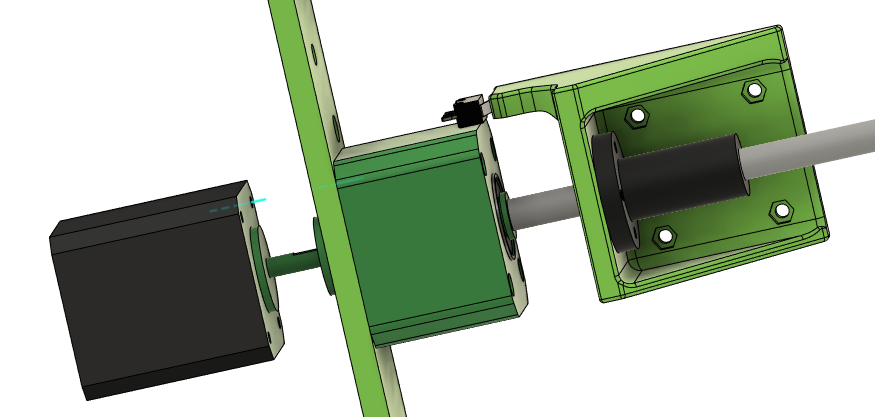
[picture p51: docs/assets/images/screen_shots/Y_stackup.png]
Y Motor Stack


Put the coupler on the motor shaft 11.5mm (ish) from the motor face

Slide the shaft collar and one M8 washer onto the leadscrew and then slide the leadscrew through the thrust block.

On the inside of the thrust block, slide the thrust bearing stack onto the lead screw and then tighten the coupler onto the lead screw.

Use 4 - M3x50 SHCS to bolt through the thrust block to the motor

Pull the lead screw away from the motor and press the shaft collar against the thrust block while tightening the set screw. - the goal is to remove the possibility for axial play. 

Y Leadnut mount - press M3 nuts into the pockets and screw to the leadnut

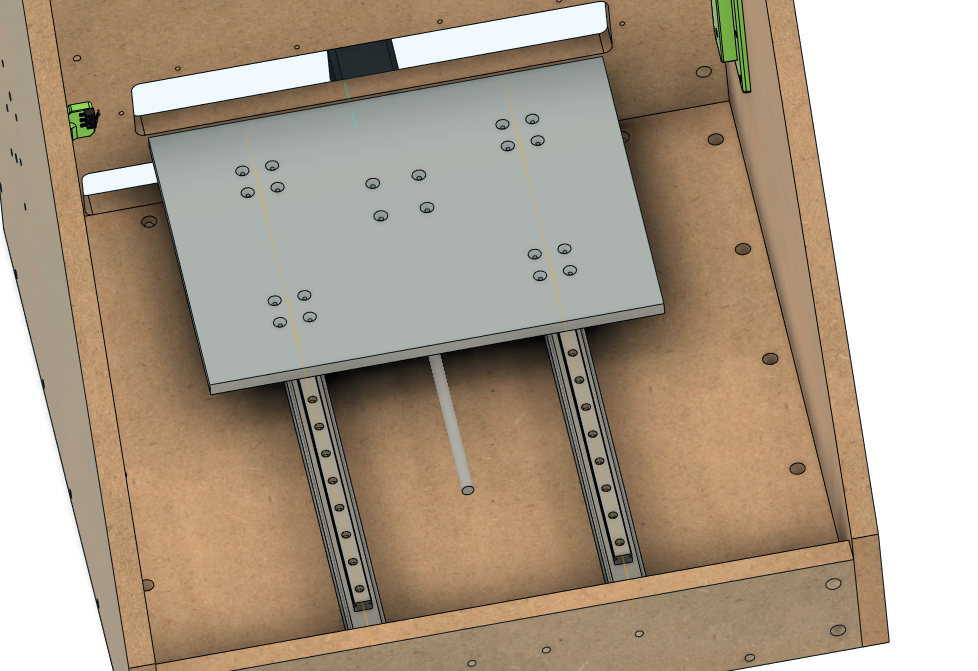
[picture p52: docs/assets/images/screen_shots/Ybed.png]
Y Axis Plate


Use M3x16 FHCS for all the carriages and lead nut mount. You may need M3x20 for the lead nut mount.

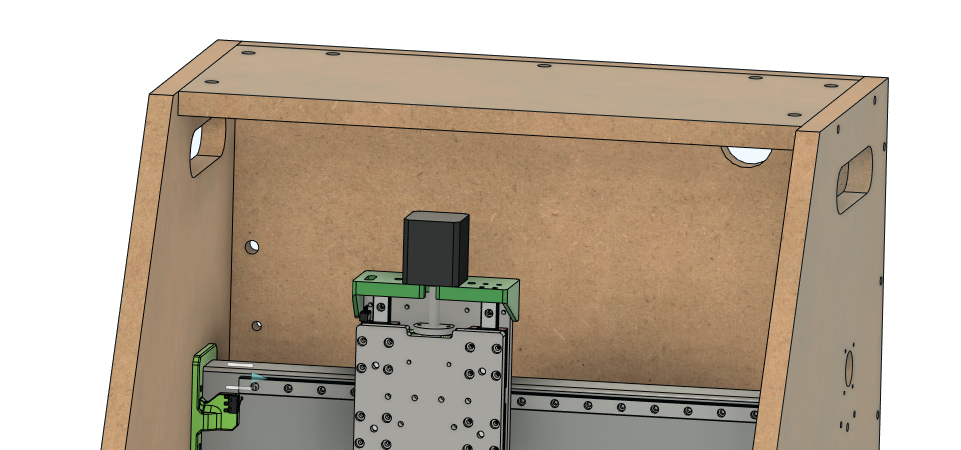
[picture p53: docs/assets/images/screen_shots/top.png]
Top


Loosen all the screws on one side to make it easier to slide the top in and loosely bolt it in.  

## Window

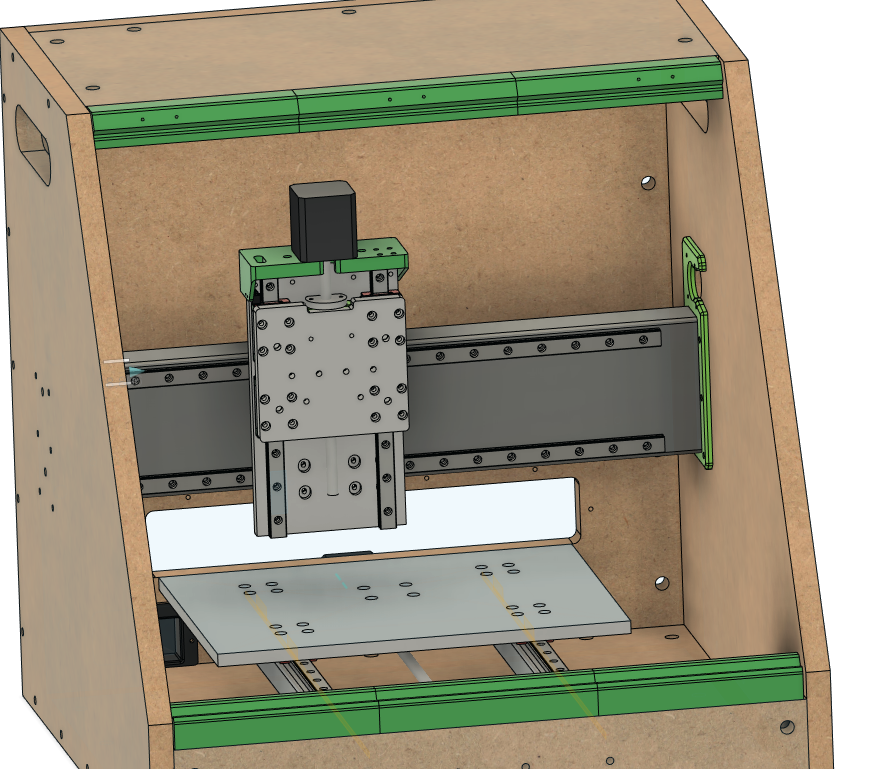
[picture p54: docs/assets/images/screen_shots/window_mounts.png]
window mounts


Screw all the window mounts to the Cr8 with 3/4" wood screws. Pay attention to the hinge mount holes on the top mounts. 

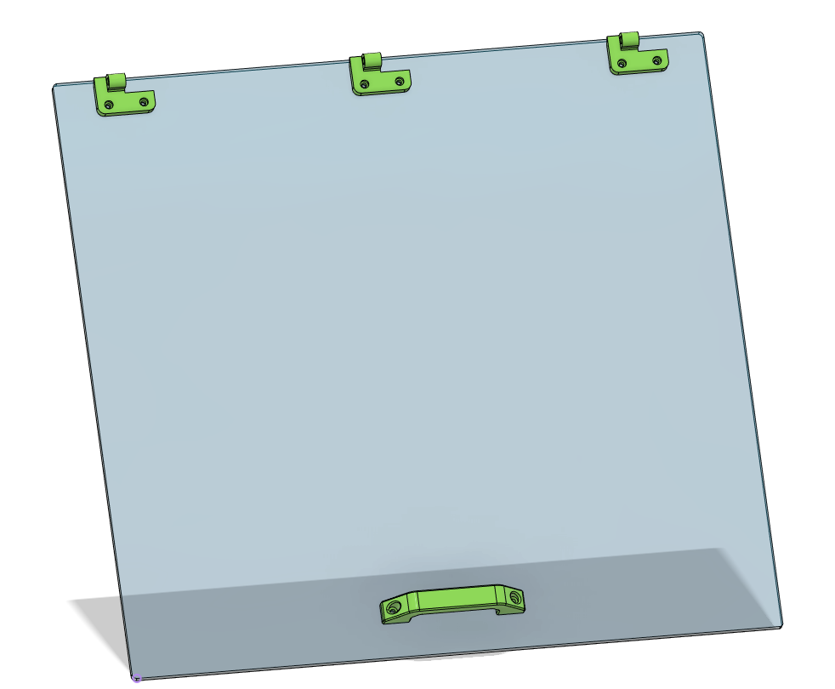
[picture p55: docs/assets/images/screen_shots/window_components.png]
window components


Use M3x12 SHCS to bolt through the window.

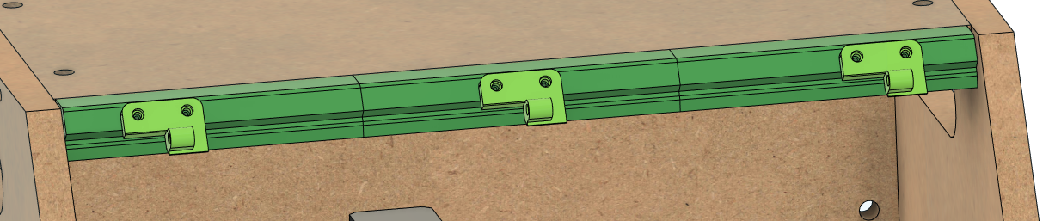
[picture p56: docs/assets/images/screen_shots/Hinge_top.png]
window hinges


Use M3 plastic tap screws or M3 SHCS to bolt the hinges to the top mounts.

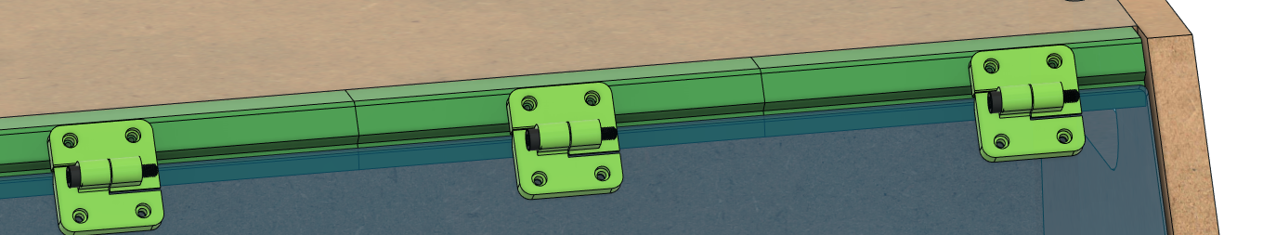
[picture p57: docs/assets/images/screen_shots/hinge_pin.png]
window pin


Use M5x25 SHCS for hinge pins

## Spindle mount

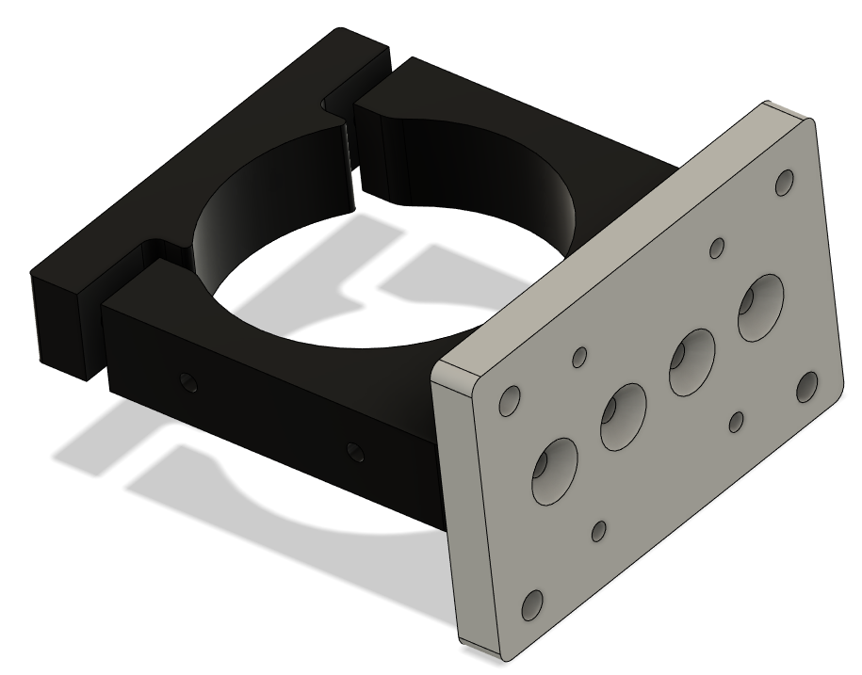
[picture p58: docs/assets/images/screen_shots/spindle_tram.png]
Spindle Mount


Use M5x20 FHCS to bolt through the back of the tram plate to the spindle mount

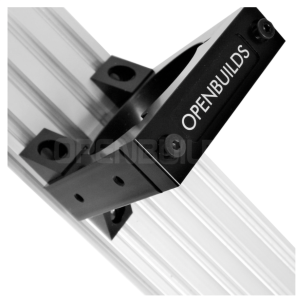
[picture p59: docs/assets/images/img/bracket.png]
Spindle Brackets


Add the 4 90-degree brackets that came with the spindle mount to the top and bottom of the mount and tram plate.

Use 4 M5x16 bolts to bolt the tram plate to the Z Plate. One of the 4 M5 holes is on size and the other 3 are overside to allow for small adjustments of tilt on the spindle

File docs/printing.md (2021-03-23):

# Print Settings
## Filament
Parts can be printed in any of these materials:

* Standard PETG
* PLA-Pro

## Perimeter

* perimeters: 4
* perimeter width: 0.56mm

## Infill

* infill: 40%
* infill type: triangle
* infill width: 0.6mm

## Layers

* layer height: 0.25mm

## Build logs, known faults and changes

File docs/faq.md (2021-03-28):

# Frequently Asked Questions

## Can it cut aluminum?
Yes. We should probably embed some youtube videos here as proof.

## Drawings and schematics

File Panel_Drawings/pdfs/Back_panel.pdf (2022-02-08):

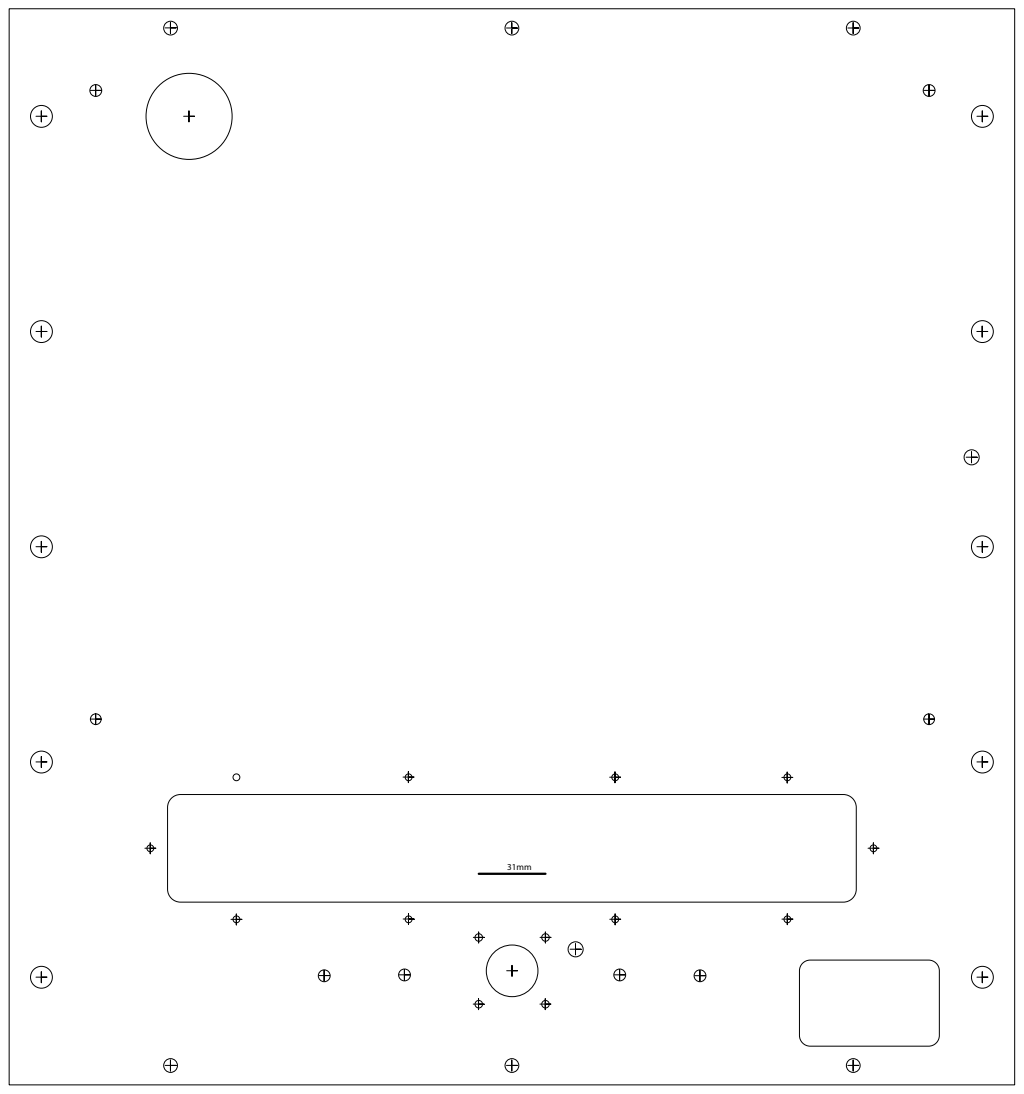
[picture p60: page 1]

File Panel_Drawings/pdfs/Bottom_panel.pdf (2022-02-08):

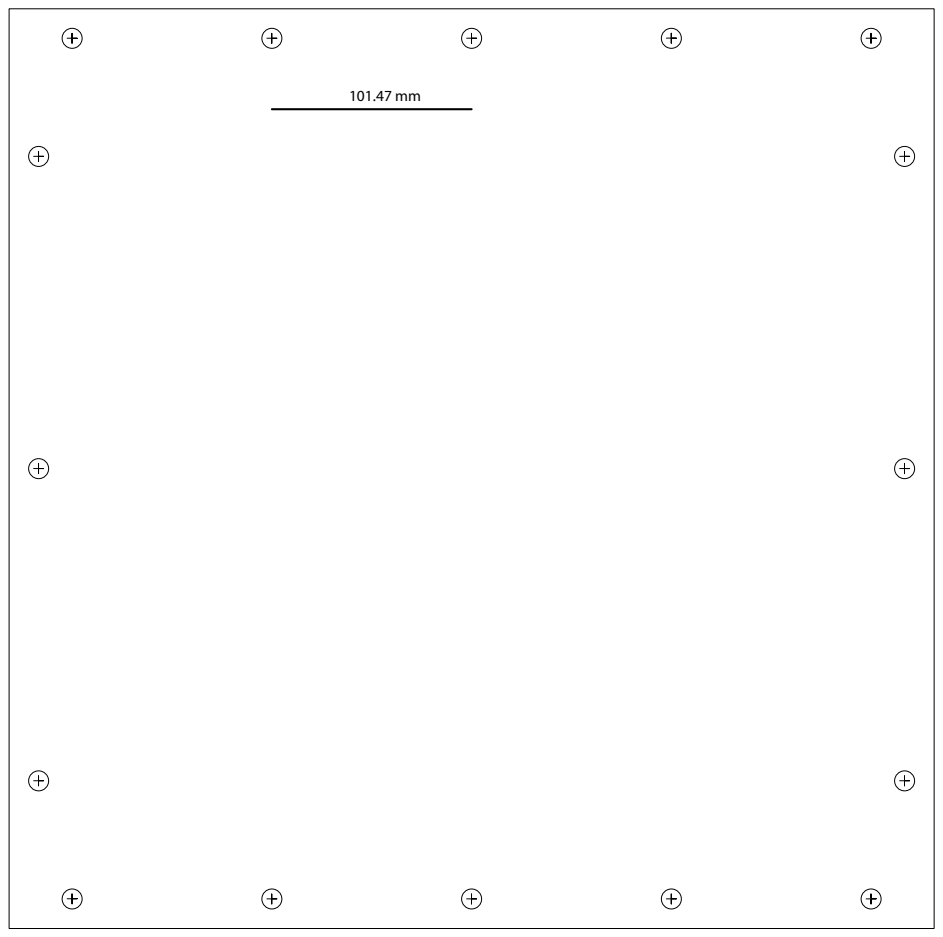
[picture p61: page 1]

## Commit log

2021-03-23 add print settings
2021-07-26 added stls and dxfs for all parts of machine
    [Back_panel.dxf, Bottom_panel.dxf, DustCover_Left.stl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]
2021-07-26 added bed punch template
    [bed_punch_template.dxf]
2021-08-05 added step and fbz files
    [DustCover_Left.step, DustCover_Right.step, Hinge_x3.step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]
2021-08-05 added github to BOM docs page
2021-08-11 added full assembly step and changed z-nut mount to be easier to tap
    [Z_Leadnut_mount.stl]
2021-10-10 added a ton and fleshed out assembly docs
2021-10-11 fixed some case issues
2021-10-12 stupid case
2022-01-07 M3 Tap Guide
    [M3TapGuide0.4mm.3mf]
2022-01-14 shimming readme
    [Back_panel.dxf, Bottom_panel.dxf, Front_panel.dxf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]
2022-01-15 correct BOM version
    [MilkCr8 BOM.xlsx]
2022-01-26 Deleted BOM
    [MilkCr8 BOM.xlsx]
2022-02-08 punch drill and tap
2022-02-09 substantial revisions to assembly
2022-02-10 major revisions to assembly, added image of spindle brackets
